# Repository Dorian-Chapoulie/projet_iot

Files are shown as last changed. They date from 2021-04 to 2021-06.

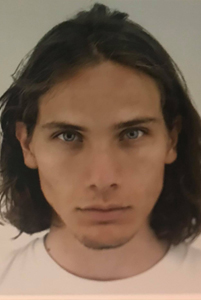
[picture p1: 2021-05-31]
Server/front/dashboard/src/assets/raph.jpg

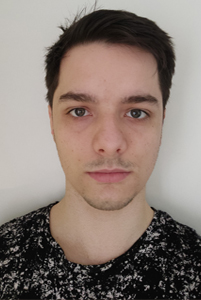
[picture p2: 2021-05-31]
Server/front/dashboard/src/assets/leo.jpg

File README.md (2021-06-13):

<p align="center">
  Sublime's custom image
</p>

<h1 align="center"> Jupiter </h1>
<h2 align="center">  Projet  IOT </h2>
<center> <h3> Février 2021 - Mai 2021 <h3> </center>
<h2 align="center">  Sous la direction de :
<br> Gilles menez</h2>

<h2 align="center">  Avec la participation de :</h2>
<center> <h3> Dorian Chapoulié <br> Rémi Longin <br> Léo Guillaumet <br> Raphael Bolier </h3> </center>

---

<h3> Table des matières </h3>

<h4>Jupiter : Présentation du projet
<br>
Jupiter : Fonctionnalités </h4>

1. Récupération de la liste des robots disponibles
2. Prise du controle d'un robot
3. Contrôle de la direction
<br>3.1 Le contrôle de la direction
<br>3.2 Le contrôle de la motorisation
<br>3.3 Le contrôle de la caméra embarquée
4. Données Publiées
5. Utilisation des données
6. Tableau des protocoles TCP

# Jupiter : Présentation du projet 

Jupiter est une mission d'exploration des locaux de la MIAGE par :
* Dorian Chapoulié
* Rémi Longin
* Léo Guillaumet
* Raphael Bolier

La mission consiste à déployer l'astromobile <b>Jupiter</b> sur le sol terrien pour étudier sa surface et collecter des données concernant la température de celle-ci.
L'objectif final est de transférer ces données à un utilisateur contrôlant le robot à distance afin d’obtenir une « heat-map » des locaux.
L’utilisateur percevra un flux vidéo généré à partir d’un ESP32-CAM installé sur Jupiter.

# Jupiter : Fonctionnalités

## 1. Récupération de la liste des robots disponibles

Nous souhaitons pouvoir choisir quel robot contrôler. Pour cela, dans ce cas notre robot sera un client MQTT qui sera abonné à un topic consacré au listage des robots.

Lorsque le robot recevra un message provenant du topic de listage, il répondra en indiquant s’il est disponible ou non (un robot est considéré disponible dès lors qu’il n’est pas entrain d’être contrôlé).

## 2. Prise du control d’un robot

Lorsqu’un utilisateur souhaite contrôler le robot depuis notre interface web, un appel sur une route sera effectué à une API en Node.JS pour que celle-ci se connecte au serveur TCP du robot. Si la connexion réussie, alors l’interface web passe en mode
« contrôle », sinon un message d’erreur est affiché.
Le front est relié à notre API grâce aux websockets. Cela permet d’envoyer les commandes au robot en temps réel.

## 3. Contrôle d’un robot

L’utilisateur peut contrôler Jupiter via notre interface web. Les contrôles sont répartis en 3 catégories :

1. Le contrôle de la direction
2. Le contrôle de la motorisation
3. Le contrôle de la caméra embarquée

### 3.1	Le contrôle de la caméra embarquée

Le contrôle de la direction se fait à l’aide des touches Q et D du clavier :

1. Q pour aller à gauche
2. D pour aller à droite

### 3.2	Le contrôle de la motorisation

Le contrôle de la motorisation se fait à l’aide des touches ESPACE/CTRL-L/Z/S du clavier :

1. ESPACE pour augmenter la vitesse
2. CTRL-L pour réduire la vitesse
3. Z pour avancer
4. S pour reculer

Lorsque le robot reçoit une instruction de contrôle de motorisation, il l’effectue pour
5 secondes. A chaque fois qu’il reçoit une instruction de ce type, le timer est remis à
0.Si le timer arrive à 5 secondes, alors le robot s’arrête jusqu’à ce qu’il reçoive une
autre instruction.
Si le robot ne reçoit pas d’instruction pendant 5 minutes, le client est déconnecté et le robot repasse en mode « disponible », et un autre utilisateur pourra en prendre le contrôle.

### 3.3	Le contrôle de la caméra embarquée

La caméra est montée sur un support comportant 2 servos moteurs, permettant un contrôle en 2 dimensions. De plus, elle enverra nombre réduit d’images par seconde afin de préserver l’autonomie de la batterie.
Le contrôle de la caméra embarquée se fait à l’aide des flèches directionnels du clavier :

1. Haut pour monter la caméra
2. Bas pour baisser la caméra
3. Droite pour tourner la caméra à droite
4. Gauche pour tourner la caméra à gauche

## 4. Données publiées

Le robot va publier périodiquement les données du capteur de température et la puissance en DB des réseaux l’entourant sur un topic MQTT.

L’API étant abonnée à ce topic, elle reçoit ces données, elle va les stocker en base, ce qui permet de générer des « heat-map » et un tracé du parcours du robot, par session.

Notre interface web sera principalement composé en plusieurs parties :

1. Le mode Contrôle
2. Affichage d'une heat-map
 
De plus, elle sera aussi abonnée au topic des données.On pourra ainsi créer un affichage de la heat-map et de la position de n’importe quel robot en temps réel, même en étant un simple spectateur.

## 5. Données publiées

Grâce à la liste en DB des réseaux aux alentours du robot, nous pouvons utiliser une triangulation de celui-ci. Nous allons donc faire une estimation de la position en fonction de la puissance des réseaux.
De plus, comme nous avons la température à une certaine position, nous pouvons générer une heat-map en temps réel.

## 6.Tableau des protocoles TCP

Nous avons créé un tableau (non définitif) des protocoles TCP utilisé pour communiquer entre le robot et l’API :

| Protocol | Description |
---------| --------- |
|I-D-< valeur> | <b>Emetteur </b> : API <br> <b>Receveur </b>: Jupiter <br> <b> Description </b> : Protocole permettant de contrôler de la direction du robot <br> <b>Paramètres </b> : Q/D <br> <b>Exemple </b> : I-D-D => aller à droite | 
|I-M-< valeur> |  <b>Emetteur </b> : API <br> <b>Receveur </b>: Jupiter <br> <b> Description </b> : Protocole permettant de contrôler la motorisation du robot <br> <b>Paramètres </b> : A/B/Z/S/C <br> <b>Exemple </b> : I-M-A => augmenter la vitesse |  
|I-C-< valeur> | <b>Emetteur </b> : API <br> <b>Receveur </b>: Jupiter <br> <b> Description </b> : Protocole permettant de contrôler la caméra du robot <br> <b>Paramètres </b> : H/B/G/D <br> <b>Exemple </b> : I-C-G => déplacer la caméra à gauche |  

## 7. Installation
  
  Uploader le code Esp/Project dans l'esp32  
  Uploader le code Esp-Cam/projet dans l'esp32CAM  
  Pour le front: Aller dans Server/front/dashboard => npm i puis npm start  
  Pour l'API: Aller dans Server/api => npm i puis npm start  
  Pour le cablage, regarder le schéma à la racine du projet  
  
  PS: Il faut renseigner le SSID et le mot de passe dans Esp/Project et Esp-Cam/projet  
  PS: vous trouverez dans le dossier "libraries" les libs utilisés dans ArduinoIDE

## 8. Sources 
  
  * heatmap.js pour la heatmap : https://www.npmjs.com/package/heatmap.js-fixed
  * react framework js :  https://www.npmjs.com/package/react
  * axios librairie servent à simplifier les requêtes HTTP : https://www.npmjs.com/package/axios
  * multer librairie pour déposer un fichier : https://www.npmjs.com/package/multer
  * mqtt librairie permettant d'utiliser le protocole mqtt : https://www.npmjs.com/package/mqtt
  * esp-ota librairie pour flash le firmware de l'esp à partir d'un fichier : https://www.npmjs.com/package/esp-ota
  * mongodb MongoDB driver permettant de se connecter à une base de donnée MongoDB : https://www.npmjs.com/package/mongodb
  * socket.io librairie qui permet une communication en temps réel, bidirectionnelle et basée sur des événements entre le navigateur et le serveur : https://www.npmjs.com/package/socket.io

  ---------
  
  librairies pour l'esp :
  
  * ArduinoJson librairie utilisée pour sérialisé ou désérialisé du Json : https://arduinojson.org/
  * AsyncTCP bibliothèque TCP entièrement asynchrone : https://github.com/me-no-dev/AsyncTCP
  * ESP32Servo-0.9.0  permet aux cartes ESP32 de contrôler des servomoteurs, des moteurs à tonalité et des moteurs à écriture analogique : https://www.arduinolibraries.info/libraries/esp32-servo
  * ESPAsyncWebServer Serveur asynchrone HTTP et WebSocket pour Arduino ESP : https://github.com/me-no-dev/ESPAsyncWebServer
  * OneWire permet l'accès aux capteurs de température, à la mémoire et à d'autres puces: https://www.arduinolibraries.info/libraries/one-wire

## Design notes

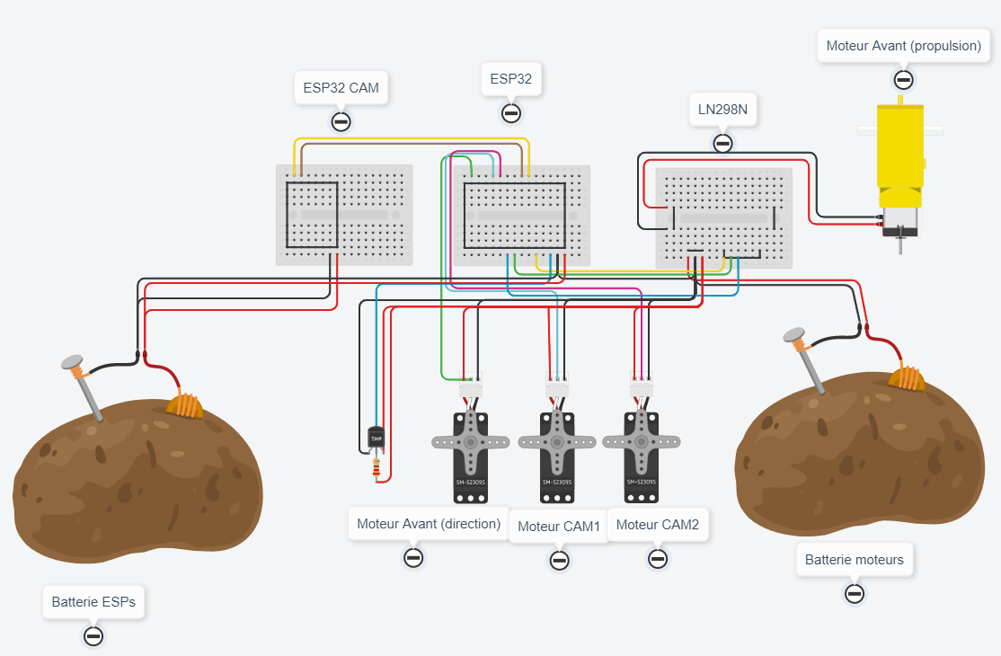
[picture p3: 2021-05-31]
Schema.PNG

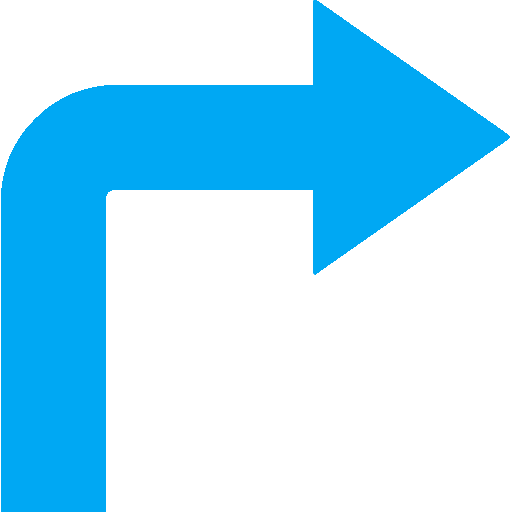
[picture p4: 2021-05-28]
Server/front/dashboard/src/assets/droite.png

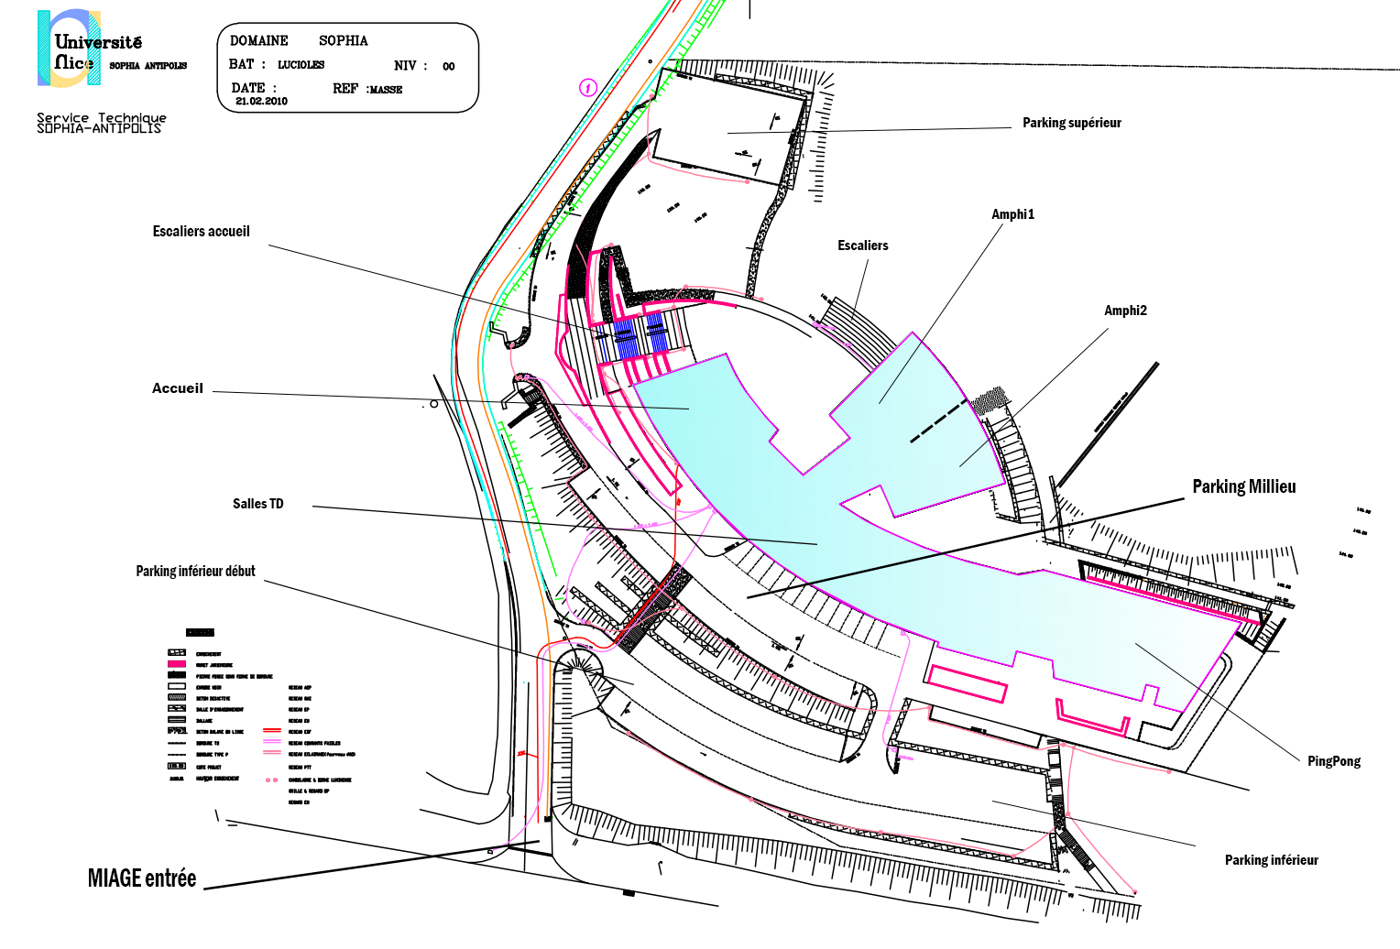
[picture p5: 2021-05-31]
Server/front/dashboard/src/assets/miage.PNG

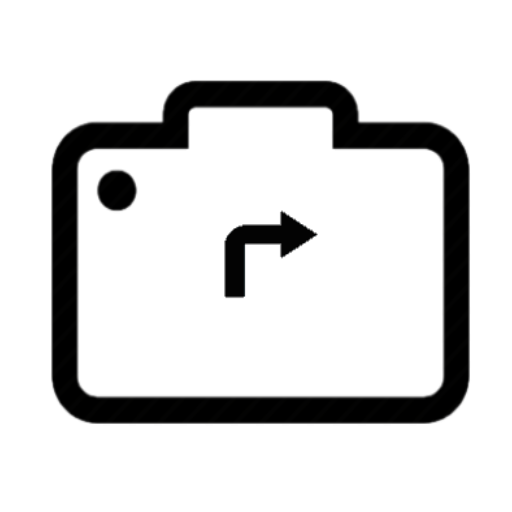
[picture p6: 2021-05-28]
Server/front/dashboard/src/assets/camRight.png

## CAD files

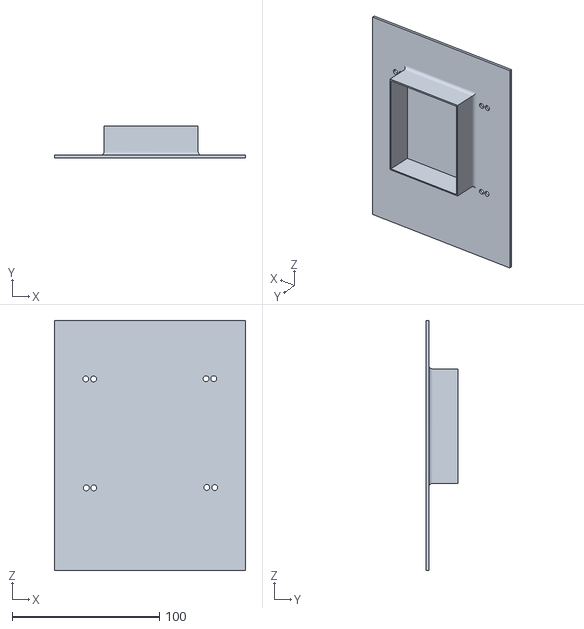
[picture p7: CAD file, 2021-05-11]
Models/main frame.stl
130.0 x 22.0 x 170.0

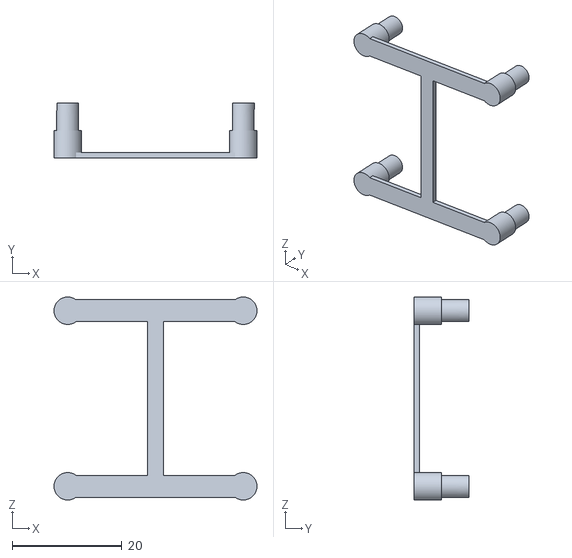
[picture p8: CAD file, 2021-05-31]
Models/support LN.stl
37.0 x 10.0 x 37.0

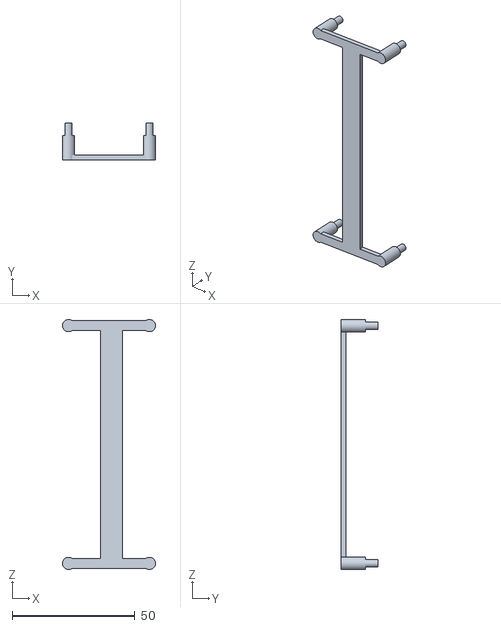
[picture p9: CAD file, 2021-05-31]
Models/support bat.stl
38.0 x 15.0 x 102.0

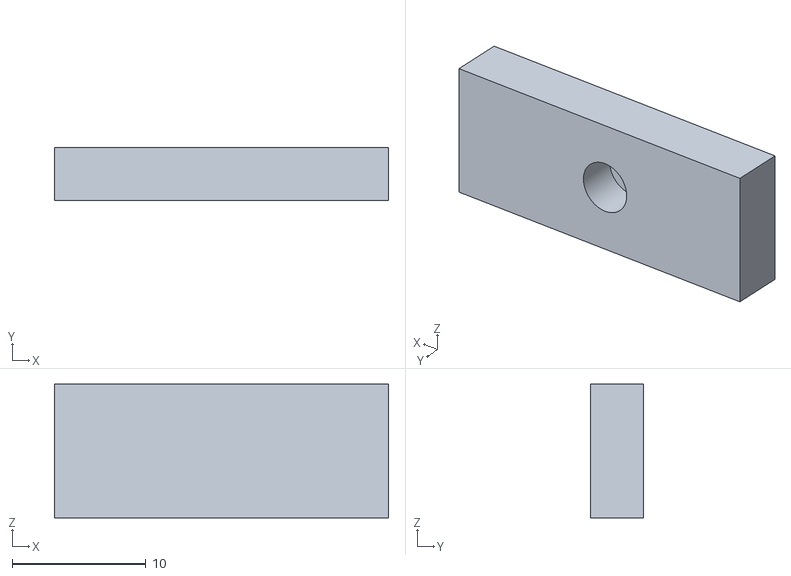
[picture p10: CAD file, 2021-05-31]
Models/support cam.stl
25.0 x 4.00 x 10.0

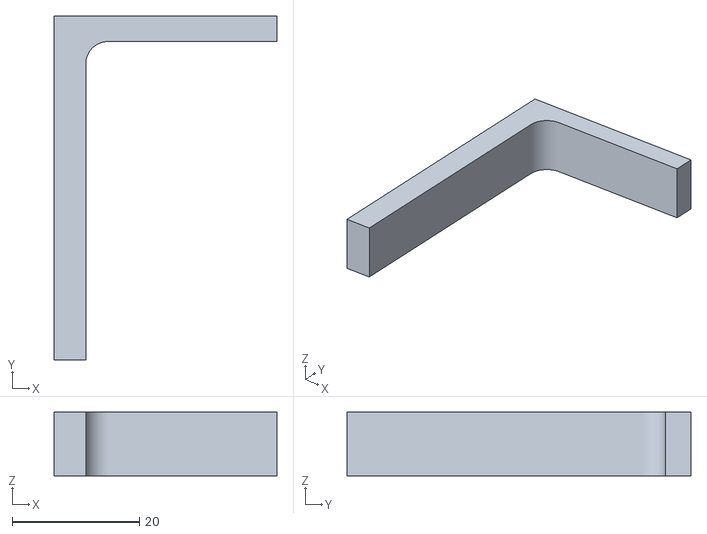
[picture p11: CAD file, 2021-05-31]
Models/support cam 2.stl
35.0 x 54.0 x 10.0

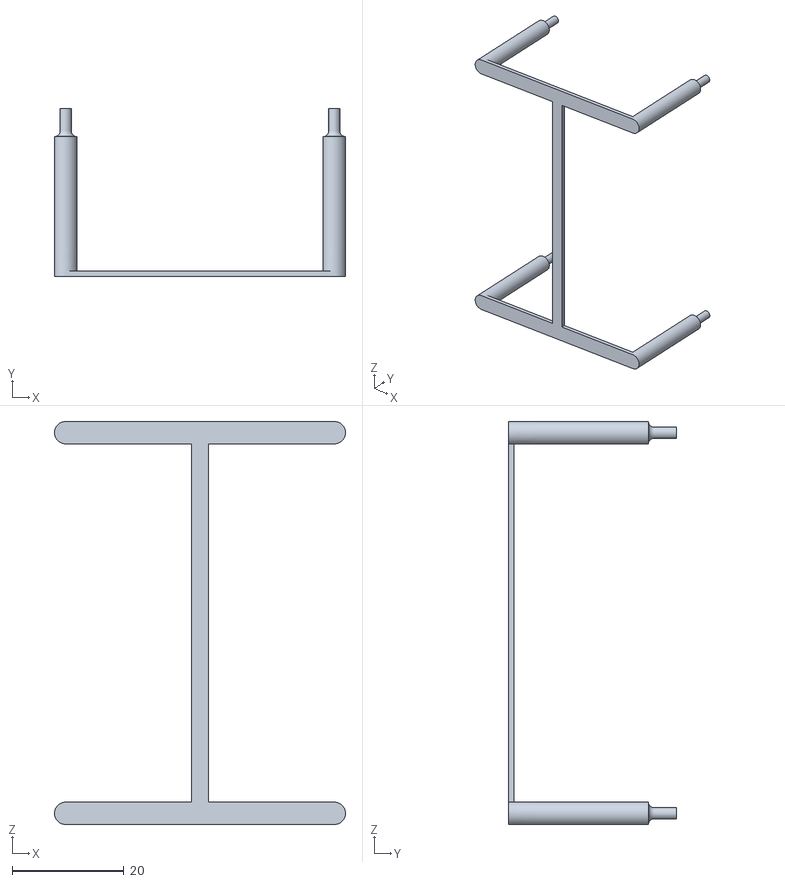
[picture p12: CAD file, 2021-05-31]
Models/support PCB.stl
52.0 x 30.0 x 72.0

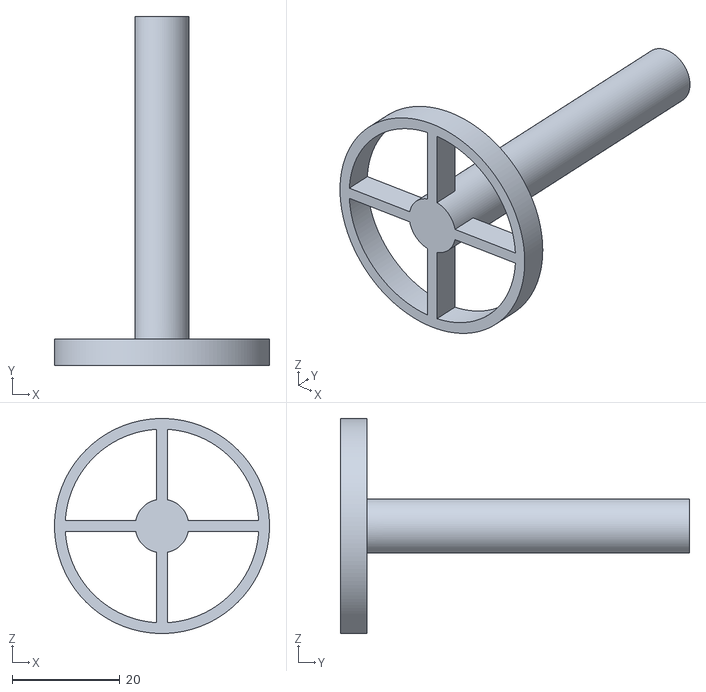
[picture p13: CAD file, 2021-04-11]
Models/roue_arriere.stl
40.0 x 65.0 x 40.0

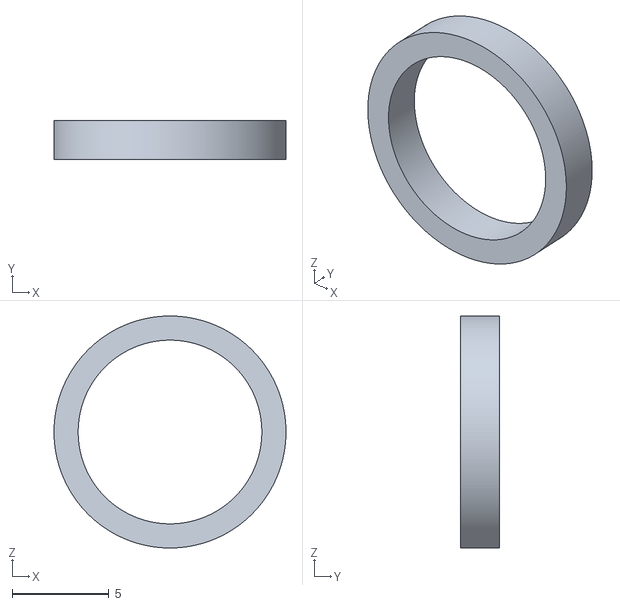
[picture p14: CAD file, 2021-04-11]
Models/ecrou roue.stl
12.0 x 2.00 x 12.0

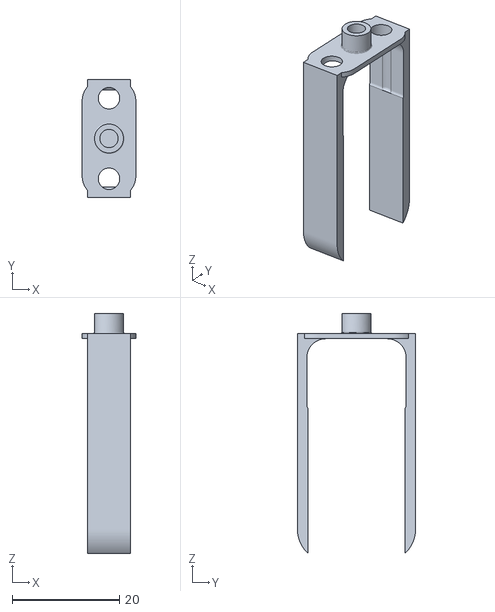
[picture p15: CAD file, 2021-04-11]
Models/etrier.stl
10.0 x 22.0 x 44.7

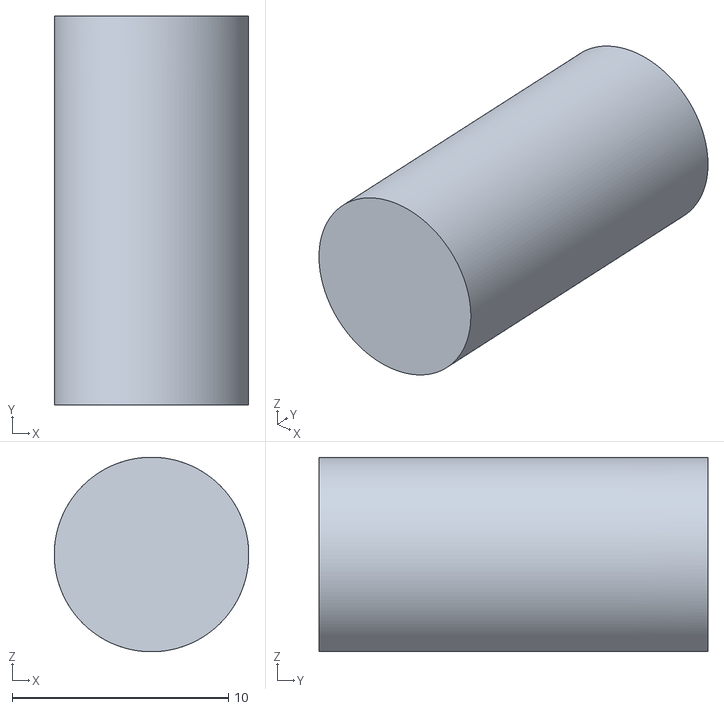
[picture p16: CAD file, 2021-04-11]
Models/cardant.stl
9.00 x 18.0 x 9.00

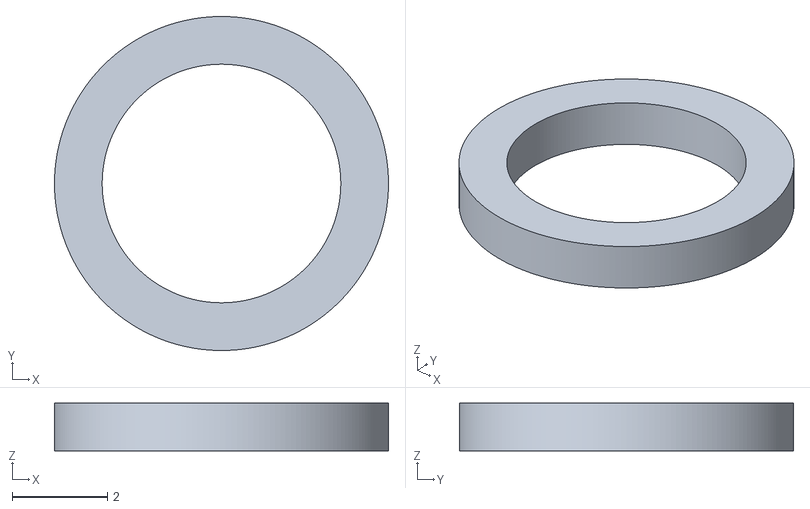
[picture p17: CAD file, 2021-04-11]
Models/ecrou_etrier.stl
7.00 x 7.00 x 1.00

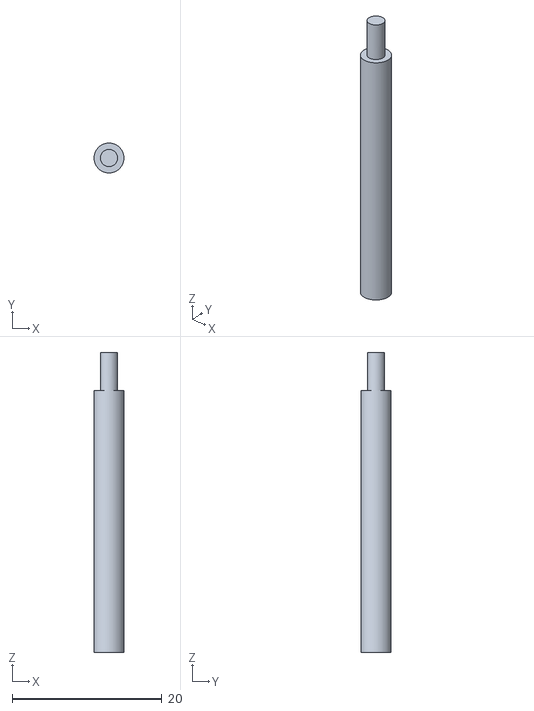
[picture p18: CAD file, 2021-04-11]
Models/support-esp.stl
4.00 x 4.00 x 40.1

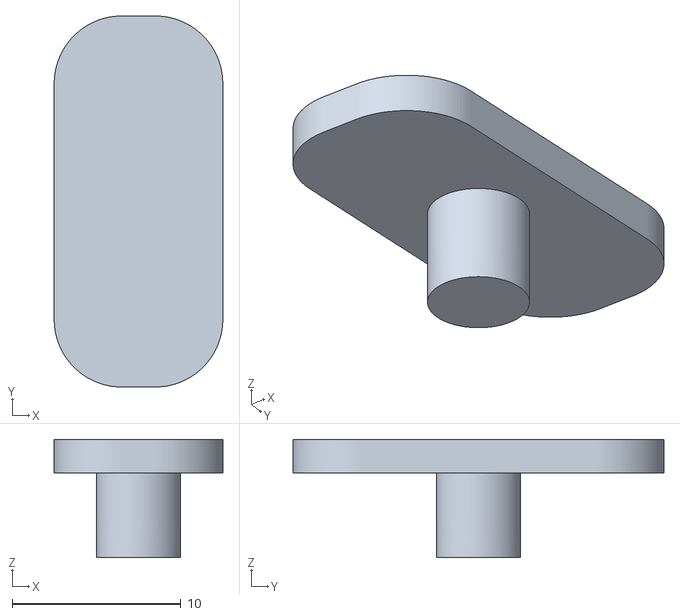
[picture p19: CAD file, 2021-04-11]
Models/attache.stl
10.0 x 22.0 x 7.00

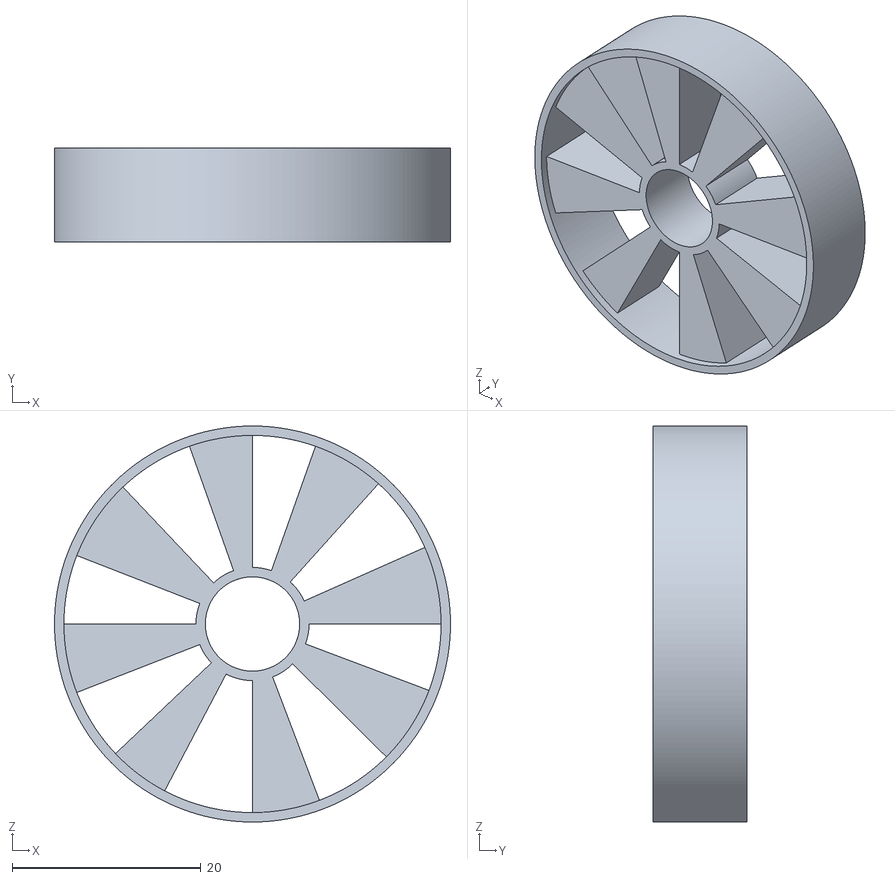
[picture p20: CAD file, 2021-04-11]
Models/roue.stl
42.0 x 10.0 x 42.0

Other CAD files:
Models/etrier_2.stl
Models/roue barre.stl

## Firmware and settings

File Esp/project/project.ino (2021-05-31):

#include <PubSubClient.h>
#include <ArduinoOTA.h>
#include <OneWire.h>
#include <DallasTemperature.h>


#include "TCPServer.hpp"
#include "Motor.hpp"
#include "Servo.hpp"
#include "mqtt.hpp"
#include "EventManager.hpp"
#include "Event.hpp"
#define RXD2 16
#define TXD2 17

const String ssid = "";
const String password = "";

TCPServer* server = TCPServer::getInstance();

Motor* motor = nullptr;
ServoHandler* servo = nullptr;
ServoHandler* servoCamHonrizon = nullptr;
ServoHandler* servoCamVertical = nullptr;
MQTTClient* mqttClient = nullptr;
EventManager* eventManager = nullptr;

const int oneWireBus = 13;     
OneWire oneWire(oneWireBus);
DallasTemperature sensors(&oneWire);

int servoPin = 22;
int servoCamHonrizonPin = 21;
int servoCamVerticalPin = 19;
int motor1Pin1 = 33;
int motor1Pin2 = 32;
int enable1Pin = 14;

String get_WifiData() {
  int numNetworks = WiFi.scanNetworks();
  String payloadWifi = "{ \"jupiterID\": \"";
  payloadWifi += WiFi.macAddress().c_str();
  payloadWifi += "\",";
  for (int i = 0; i < numNetworks; i++) {
    payloadWifi += '"' + WiFi.BSSIDstr(i) + '"' + ":" + '"'+WiFi.RSSI(i)+'"'+ ",\n";
  }
 
  return payloadWifi;
}


void setup() {
  Serial.begin(9600);
  WiFi.mode(WIFI_STA);
  Serial2.begin(9600, SERIAL_8N1, RXD2, TXD2);
  sensors.begin();
  
  TCPServer::init(25565, ssid, password);
  MQTTClient::init(ssid, password);

  mqttClient = MQTTClient::getInstance();
  eventManager = EventManager::getInstance();

  motor = new Motor(motor1Pin1, motor1Pin2, enable1Pin);
  servo = new ServoHandler(servoPin);
  servoCamHonrizon = new ServoHandler(servoCamHonrizonPin);
  servoCamVertical = new ServoHandler(servoCamVerticalPin);

  /* ------- SENS ------*/
  eventManager->setEventListener("turn_r", [](EventCallbackData& d){
    servo->turnRight();
  });
  eventManager->setEventListener("turn_l", [](EventCallbackData& d){
    servo->turnLeft();
  });
  
  /* ------- VITESSE ------*/
  eventManager->setEventListener("speed_i", [](EventCallbackData& d){
    motor->increaseSpeed();
  });
  eventManager->setEventListener("speed_d", [](EventCallbackData& d){
    motor->decreaseSpeed();
  });

  /* ------- DIRECTION ------*/
  eventManager->setEventListener("forward", [](EventCallbackData& d){
    motor->forward();
  });
  eventManager->setEventListener("backward", [](EventCallbackData& d){
    motor->backward();
  });
  eventManager->setEventListener("stop", [](EventCallbackData& d){
    motor->stop();
  });
  
  /* ------- CAM HONRIZONTAL ------*/
  eventManager->setEventListener("turn_cam_r", [](EventCallbackData& d){
    servoCamHonrizon->turnRight();
  });
  eventManager->setEventListener("turn_cam_d", [](EventCallbackData& d){
    servoCamHonrizon->turnLeft();
  });
  
  /* ------- CAM VERTICAL ------*/
  eventManager->setEventListener("turn_cam_u", [](EventCallbackData& d){
    servoCamVertical->turnRight();
  });
  eventManager->setEventListener("turn_cam_b", [](EventCallbackData& d){
    servoCamVertical->turnLeft();
  });
  
  ArduinoOTA.setPassword("2a6d8ad0-9Ef;!&");
  ArduinoOTA.begin();
}

String command;
String payload;
int sendData = 0;
EventCallbackData data;

void loop() {
  mqttClient->loop();
  ArduinoOTA.handle();
   while (Serial2.available() /*&& mqttClient->camIp.length() <= 0*/) {
    command = Serial2.readStringUntil('\n');
    mqttClient->camIp = command.substring(0, command.length() - 1);
  }

  if (sendData >= 60) {
    sensors.requestTemperatures(); 
    float temperatureC = sensors.getTempCByIndex(0);
    payload = get_WifiData();
    payload += "\"temp\":\"" + String(temperatureC) + "\"}";
    char data[payload.length() + 1];
    payload.toCharArray(data, (payload.length() + 1));
    MQTTClient::getInstance()->m_mqttClient->publish(MQTTClient::getInstance()->m_pubTopics[2], data);
    sendData = 0;
  }

  data.iValue = TCPServer::getInstance()->getIsAvailable() ? 1 : 0;
  eventManager->trigerEvent("isavailable", data);
 
  sendData++;
  delay(500);
}

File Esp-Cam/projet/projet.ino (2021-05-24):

/*********
  Rui Santos
  Complete project details at https://RandomNerdTutorials.com/esp32-cam-video-streaming-web-server-camera-home-assistant/
  
  IMPORTANT!!! 
   - Select Board "AI Thinker ESP32-CAM"
   - GPIO 0 must be connected to GND to upload a sketch
   - After connecting GPIO 0 to GND, press the ESP32-CAM on-board RESET button to put your board in flashing mode
  
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
  The above copyright notice and this permission notice shall be included in all
  copies or substantial portions of the Software.
*********/

#include "esp_camera.h"
#include <WiFi.h>
#include "esp_timer.h"
#include "img_converters.h"
#include "Arduino.h"
#include "fb_gfx.h"
#include "soc/soc.h" //disable brownout problems
#include "soc/rtc_cntl_reg.h"  //disable brownout problems
#include "esp_http_server.h"

//Replace with your network credentials
const char* ssid = "";
const char* password = "";

#define PART_BOUNDARY "123456789000000000000987654321"

// This project was tested with the AI Thinker Model, M5STACK PSRAM Model and M5STACK WITHOUT PSRAM
#define CAMERA_MODEL_AI_THINKER
//#define CAMERA_MODEL_M5STACK_PSRAM
//#define CAMERA_MODEL_M5STACK_WITHOUT_PSRAM

// Not tested with this model
//#define CAMERA_MODEL_WROVER_KIT

#if defined(CAMERA_MODEL_WROVER_KIT)
  #define PWDN_GPIO_NUM    -1
  #define RESET_GPIO_NUM   -1
  #define XCLK_GPIO_NUM    21
  #define SIOD_GPIO_NUM    26
  #define SIOC_GPIO_NUM    27
  
  #define Y9_GPIO_NUM      35
  #define Y8_GPIO_NUM      34
  #define Y7_GPIO_NUM      39
  #define Y6_GPIO_NUM      36
  #define Y5_GPIO_NUM      19
  #define Y4_GPIO_NUM      18
  #define Y3_GPIO_NUM       5
  #define Y2_GPIO_NUM       4
  #define VSYNC_GPIO_NUM   25
  #define HREF_GPIO_NUM    23
  #define PCLK_GPIO_NUM    22

#elif defined(CAMERA_MODEL_M5STACK_PSRAM)
  #define PWDN_GPIO_NUM     -1
  #define RESET_GPIO_NUM    15
  #define XCLK_GPIO_NUM     27
  #define SIOD_GPIO_NUM     25
  #define SIOC_GPIO_NUM     23
  
  #define Y9_GPIO_NUM       19
  #define Y8_GPIO_NUM       36
  #define Y7_GPIO_NUM       18
  #define Y6_GPIO_NUM       39
  #define Y5_GPIO_NUM        5
  #define Y4_GPIO_NUM       34
  #define Y3_GPIO_NUM       35
  #define Y2_GPIO_NUM       32
  #define VSYNC_GPIO_NUM    22
  #define HREF_GPIO_NUM     26
  #define PCLK_GPIO_NUM     21

#elif defined(CAMERA_MODEL_M5STACK_WITHOUT_PSRAM)
  #define PWDN_GPIO_NUM     -1
  #define RESET_GPIO_NUM    15
  #define XCLK_GPIO_NUM     27
  #define SIOD_GPIO_NUM     25
  #define SIOC_GPIO_NUM     23
  
  #define Y9_GPIO_NUM       19
  #define Y8_GPIO_NUM       36
  #define Y7_GPIO_NUM       18
  #define Y6_GPIO_NUM       39
  #define Y5_GPIO_NUM        5
  #define Y4_GPIO_NUM       34
  #define Y3_GPIO_NUM       35
  #define Y2_GPIO_NUM       17
  #define VSYNC_GPIO_NUM    22
  #define HREF_GPIO_NUM     26
  #define PCLK_GPIO_NUM     21

#elif defined(CAMERA_MODEL_AI_THINKER)
  #define PWDN_GPIO_NUM     32
  #define RESET_GPIO_NUM    -1
  #define XCLK_GPIO_NUM      0
  #define SIOD_GPIO_NUM     26
  #define SIOC_GPIO_NUM     27
  
  #define Y9_GPIO_NUM       35
  #define Y8_GPIO_NUM       34
  #define Y7_GPIO_NUM       39
  #define Y6_GPIO_NUM       36
  #define Y5_GPIO_NUM       21
  #define Y4_GPIO_NUM       19
  #define Y3_GPIO_NUM       18
  #define Y2_GPIO_NUM        5
  #define VSYNC_GPIO_NUM    25
  #define HREF_GPIO_NUM     23
  #define PCLK_GPIO_NUM     22
#else
  #error "Camera model not selected"
#endif

static const char* _STREAM_CONTENT_TYPE = "multipart/x-mixed-replace;boundary=" PART_BOUNDARY;
static const char* _STREAM_BOUNDARY = "\r\n--" PART_BOUNDARY "\r\n";
static const char* _STREAM_PART = "Content-Type: image/jpeg\r\nContent-Length: %u\r\n\r\n";

httpd_handle_t stream_httpd = NULL;

static esp_err_t stream_handler(httpd_req_t *req){
  camera_fb_t * fb = NULL;
  esp_err_t res = ESP_OK;
  size_t _jpg_buf_len = 0;
  uint8_t * _jpg_buf = NULL;
  char * part_buf[64];

  res = httpd_resp_set_type(req, _STREAM_CONTENT_TYPE);
  if(res != ESP_OK){
    return res;
  }

  while(true){
    fb = esp_camera_fb_get();
    if (!fb) {
      //Serial.println("Camera capture failed");
      res = ESP_FAIL;
    } else {
      if(fb->width > 400){
        if(fb->format != PIXFORMAT_JPEG){
          bool jpeg_converted = frame2jpg(fb, 80, &_jpg_buf, &_jpg_buf_len);
          esp_camera_fb_return(fb);
          fb = NULL;
          if(!jpeg_converted){
            //Serial.println("JPEG compression failed");
            res = ESP_FAIL;
          }
        } else {
          _jpg_buf_len = fb->len;
          _jpg_buf = fb->buf;
        }
      }
    }
    if(res == ESP_OK){
      size_t hlen = snprintf((char *)part_buf, 64, _STREAM_PART, _jpg_buf_len);
      res = httpd_resp_send_chunk(req, (const char *)part_buf, hlen);
    }
    if(res == ESP_OK){
      res = httpd_resp_send_chunk(req, (const char *)_jpg_buf, _jpg_buf_len);
    }
    if(res == ESP_OK){
      res = httpd_resp_send_chunk(req, _STREAM_BOUNDARY, strlen(_STREAM_BOUNDARY));
    }
    if(fb){
      esp_camera_fb_return(fb);
      fb = NULL;
      _jpg_buf = NULL;
    } else if(_jpg_buf){
      free(_jpg_buf);
      _jpg_buf = NULL;
    }
    if(res != ESP_OK){
      break;
    }
    //Serial.printf("MJPG: %uB\n",(uint32_t)(_jpg_buf_len));
  }
  return res;
}

void startCameraServer(){
  httpd_config_t config = HTTPD_DEFAULT_CONFIG();
  config.server_port = 80;

  httpd_uri_t index_uri = {
    .uri       = "/",
    .method    = HTTP_GET,
    .handler   = stream_handler,
    .user_ctx  = NULL
  };
  
  //Serial.printf("Starting web server on port: '%d'\n", config.server_port);
  if (httpd_start(&stream_httpd, &config) == ESP_OK) {
    httpd_register_uri_handler(stream_httpd, &index_uri);
  }
}
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

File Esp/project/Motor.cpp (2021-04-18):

 #include "Motor.hpp"
 
Motor::Motor(const byte motor1Pin1, const byte motor1Pin2, const byte enablePin) {
  m_motor1Pin1 = motor1Pin1;
  m_motor1Pin2 = motor1Pin2;
  init(enablePin);
}

Motor::~Motor() {

}

void Motor::init(const byte enablePin) {
  pinMode(m_motor1Pin1, OUTPUT);
  pinMode(m_motor1Pin2, OUTPUT);
  pinMode(enablePin, OUTPUT);  
  ledcSetup(m_pwmChannel, m_freq, m_resolution);
  ledcAttachPin(enablePin, m_pwmChannel);
  ledcWrite(m_pwmChannel, m_speed);
}

void Motor::forward() {
  digitalWrite(m_motor1Pin1, LOW);
  digitalWrite(m_motor1Pin2, HIGH);
}
void Motor::backward(){
  digitalWrite(m_motor1Pin1, HIGH);
  digitalWrite(m_motor1Pin2, LOW);
}
void Motor::stop() {
  digitalWrite(m_motor1Pin1, LOW);
  digitalWrite(m_motor1Pin2, LOW);
}
void Motor::increaseSpeed(){
  if (m_speed + m_speedStep <= 255) {
    m_speed += m_speedStep;
  }
  ledcWrite(m_pwmChannel, m_speed);
}
void Motor::decreaseSpeed(){
  if (m_speed - m_speedStep >= 0) {
    m_speed -= m_speedStep;
  }
  ledcWrite(m_pwmChannel, m_speed);
}

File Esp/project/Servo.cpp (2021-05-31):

 #include "Servo.hpp"

unsigned int ServoHandler::m_pwmChannel = 1;
ServoHandler::ServoHandler(const byte pin) {
  pinMode(pin, OUTPUT);
  ledcSetup(m_pwmChannel++, m_freq, m_resolution);
  ledcAttachPin(pin, m_pwmChannel);
  servo.attach(pin);
  //rotate(m_position);
}

ServoHandler::~ServoHandler() {

}

void ServoHandler::rotate(byte position) {
  servo.write(position);
}

void ServoHandler::turnLeft() {
  if (m_position - m_turnStep >= 60) {
     m_position -= m_turnStep;
  }
  servo.write(m_position);
}

void ServoHandler::turnRight() {
  if (m_position + m_turnStep <= 130) {
     m_position += m_turnStep;
  }
  servo.write(m_position);
}

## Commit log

2021-04-18 esp: clean code and fix tcp server
    [Motor.cpp, Servo.cpp]
2021-04-20 adding camera control
    [support_cam.stl]
2021-05-08 Change design button, add return button page and add controls modal
2021-05-11 update robot main frame
    [main frame.stl]
2021-05-24 adding camera
2021-05-28 Add progressbar turning camera and image direction
2021-05-30 feat(front): add HeatMap view
2021-05-31 adding heatmap WIP
    [support PCB.stl]
2021-05-31 replace ssid by bssid
    [project.ino]
2021-05-31 adding heatmap
2021-05-31 Add buton link heatMap
2021-05-31 fix mqtt buffer size
    [project.ino]
2021-05-31 adding excel
    [M1Miage_2021.xls]
2021-05-31 adding stuff
    [support cam 2.stl, support cam.stl, support_cam.stl]
2021-05-31 removing estimated pos and adding models
    [support LN.stl, support bat.stl]
2021-05-31 adding libs for arduino ide
2021-06-13 Ajout de la présentation
2021-06-13 update read me add sources & heatmap sources
